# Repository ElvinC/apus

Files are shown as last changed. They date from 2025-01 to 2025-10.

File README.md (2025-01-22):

# The Apus Flight Computer (Work in progress and untested!)

Just a smol board for rockets.

Basically the [rocketbeacon](https://github.com/ElvinC/rocketbeacon) with added deployment channels and sensors.

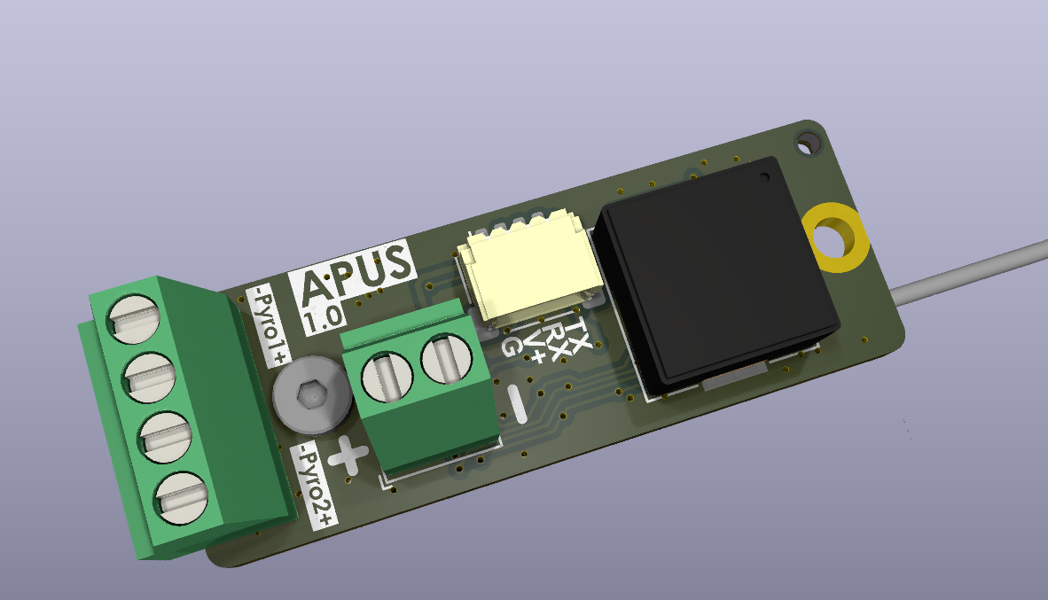
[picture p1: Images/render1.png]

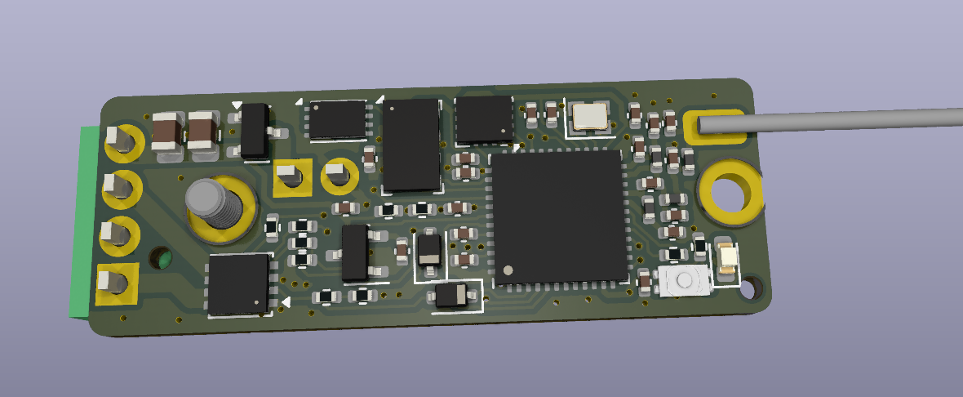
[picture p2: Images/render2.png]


Rev. 1.0 has the following hardware:

* STM32WLE5 MCU Built-in sub-GHz transceiver (for telemetry or RDF) tuned for the 440MHz band
* 2x pyro deployment channels with continuity detection
* 16Mbit flash (W25Q16JVUXIQ)
* BMI270 IMU
* MS5607 Barometer
* Reverse voltage protection
* 13x36mm board size with 2x M2 mounting holes

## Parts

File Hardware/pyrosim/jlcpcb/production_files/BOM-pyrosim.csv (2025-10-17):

Comment | Designator | Footprint | LCSC | Quantity
470R | R4 | R_0603_1608Metric |  | 1
Conn_01x04_Pin | J1 | PinHeader_1x04_P2.54mm_Horizontal |  | 1
470R | R3 | R_0603_1608Metric |  | 1
LED | D1 | LED_0603_1608Metric |  | 1
470R | R2 | R_0603_1608Metric |  | 1
470R | R1 | R_0603_1608Metric |  | 1
LED | D2 | LED_0603_1608Metric |  | 1

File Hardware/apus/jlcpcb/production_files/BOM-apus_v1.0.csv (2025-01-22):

Comment | Designator | Footprint | LCSC | Quantity
STM32WLE5CBUx | U1 | QFN-48-1EP_7x7mm_P0.5mm_EP5.6x5.6mm | C1121847 | 1
1k | R10,R9 | R_0402_1005Metric | C11702 | 2
68p | C4 | C_0402_1005Metric | C14441 | 1
100u | C17,C19 | C_0805_2012Metric | C15008 | 2
AO3401A | Q1 | SOT-23 | C15127 | 1
15p | C7 | C_0402_1005Metric | C1548 | 1
10u | C1,C10,C11,C12,C13,C14,C15,C2,C3 | C_0402_1005Metric | C15525 | 9
2.7p | C6 | C_0402_1005Metric | C1561 | 1
6.8p | C8 | C_0402_1005Metric | C1576 | 1
3.6p | C20 | C_0402_1005Metric | C161321 | 1
1N5819WS | D2,D3 | D_SOD-323 | C191023 | 2
RED | D1 | LED_0603_1608Metric | C2286 | 1
10k | R1,R2,R5,R6,R7,R8 | R_0402_1005Metric | C25744 | 6
33k | R4 | R_0402_1005Metric | C25779 | 1
4k7 | R3 | R_0402_1005Metric | C25900 | 1
10n | L2 | L_0402_1005Metric | C27147 | 1
47n | C5 | C_0402_1005Metric | C272875 | 1
BMI270 | U6 | Bosch_LGA-14_3x2.5mm_P0.5mm | C2836813 | 1
W25Q16JVUXIQ | U4 | Winbond_USON-8-1EP_3x2mm_P0.5mm_EP0.2x1.6mm | C2843335 | 1
32MHz | Y1 | Crystal_SMD_2016-4Pin_2.0x1.6mm | C383840 | 1
470n | C9 | C_0402_1005Metric | C47339 | 1
1u | C16,C18 | C_0402_1005Metric | C52923 | 2
4p | C21 | C_0402_1005Metric | C541337 | 1
XC6206P332MR | U2 | SOT-23 | C5446 | 1
18n | L3 | L_0402_1005Metric | C86060 | 1
BOOT | SW1 | SW_1TS026A | C913778 | 1
Pyros | J3 | TerminalBlock_Phoenix_MPT-0,5-4-2.54_1x04_P2.54mm_Horizontal | C918122 | 1
YJQ3622A | Q2 | Vishay_PowerPAK_1212-8_Dual | C919566 | 1
68n | L1 | L_0402_1005Metric | C98000 | 1
MS5607-02BA | U3 | LGA-8_3x5mm_P1.25mm | C9900023641 | 1
Conn_01x04_Socket | J1 | JST_SH_SM04B-SRSS-TB_1x04-1MP_P1.00mm_Horizontal |  | 1
lipo | BT1 | TerminalBlock_TE_282834-2_1x02_P2.54mm_Horizontal |  | 1
30n | L4 | L_0402_1005Metric |  | 1
Buzzer | BZ1 | Buzzer_Murata_PKMCS0909E |  | 1

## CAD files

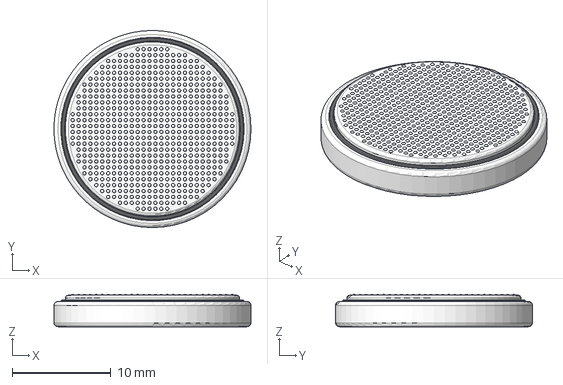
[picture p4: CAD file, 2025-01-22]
Hardware/apus/3dmodels/cr2032_cell.step
20.0 x 20.0 x 3.30 mm

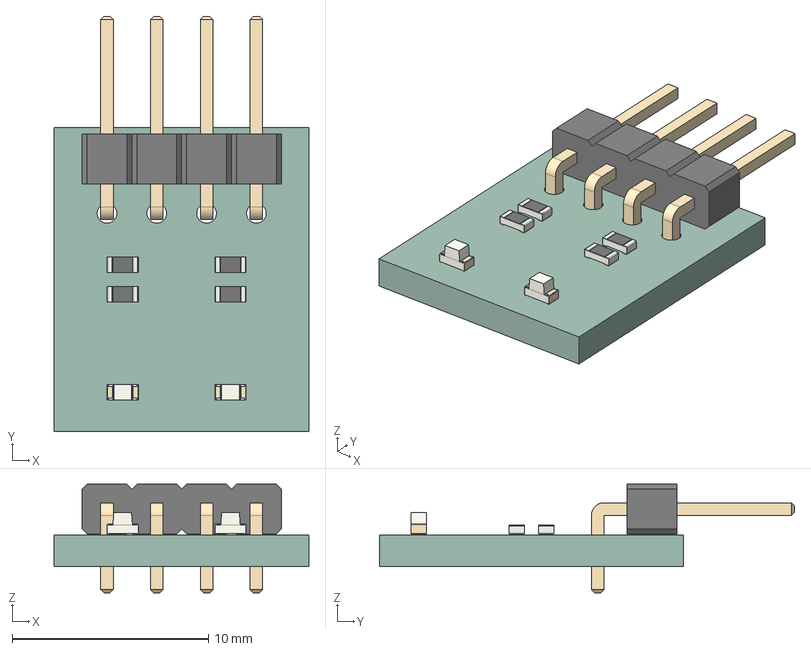
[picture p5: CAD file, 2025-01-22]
Hardware/pyrosim/pyrosim.step
13.0 x 21.2 x 5.54 mm
R_0603_1608Metric x 4
PinHeader_1x04_P254mm_Horizontal
LED_0603_1608Metric x 2
pyrosim_PCB

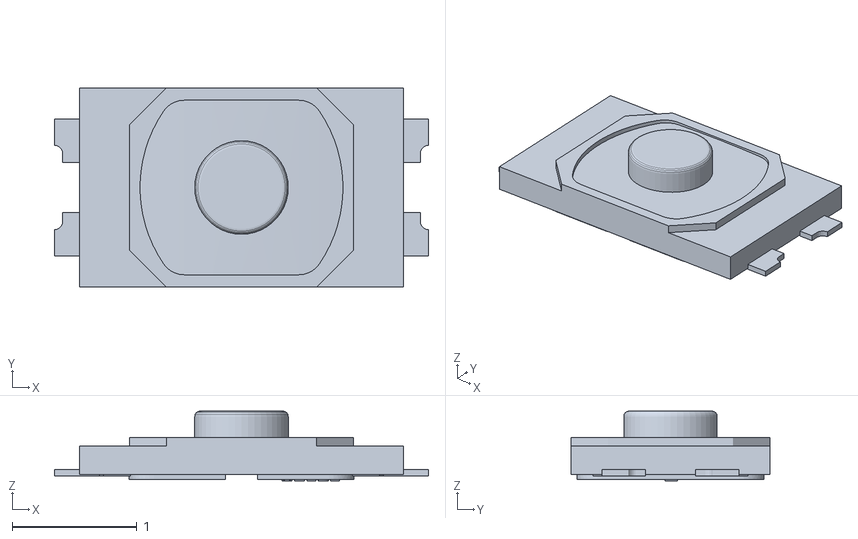
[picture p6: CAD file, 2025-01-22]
Hardware/apus/3dmodels/1TS026A-1000-0550-CT.obj
3.00 x 1.60 x 0.56

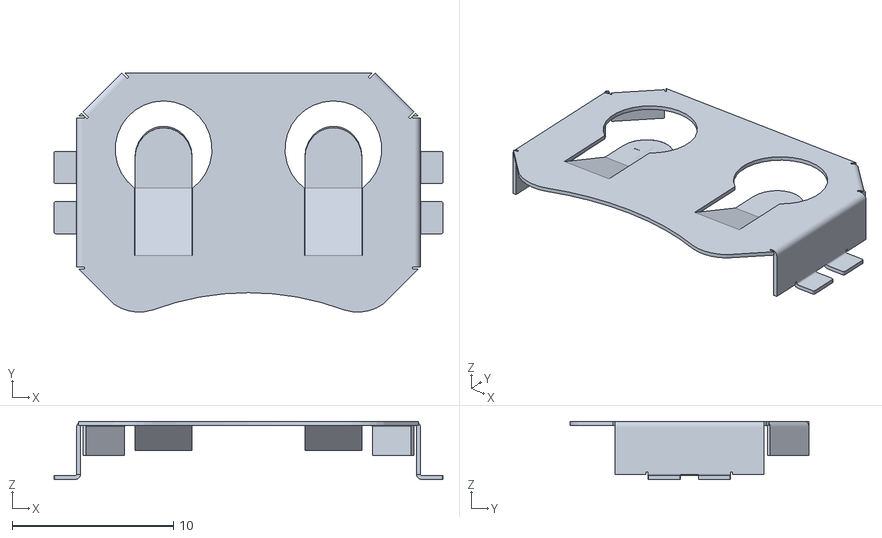
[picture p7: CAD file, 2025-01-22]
Hardware/apus/3dmodels/cr2032.obj
24.1 x 14.8 x 3.60

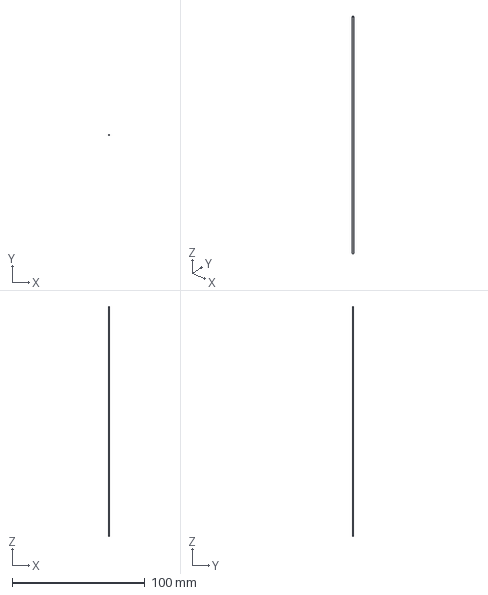
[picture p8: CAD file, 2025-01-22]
Hardware/apus/3dmodels/whipantenna.step
0.999 x 1 x 173.0 mm

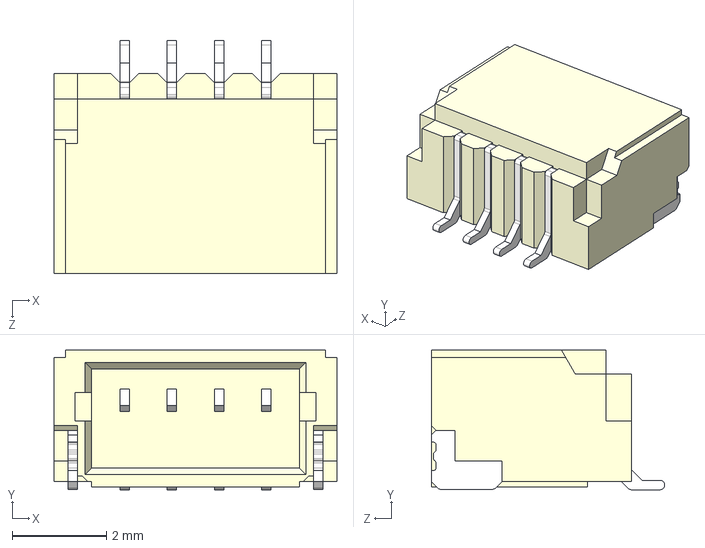
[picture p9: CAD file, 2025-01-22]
Hardware/apus/3dmodels/SM04B-SRSS-TB (LF)(SN)--3DModel-STEP-269445.STEP
6.00 x 2.96 x 4.95 mm

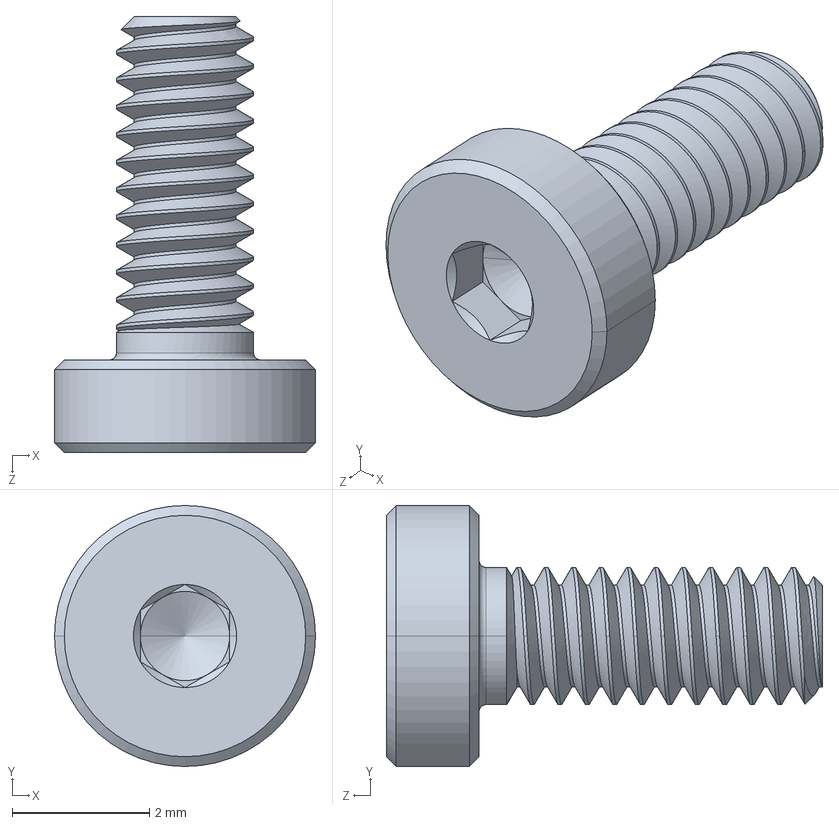
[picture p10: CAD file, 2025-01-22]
Hardware/apus/3dmodels/92855A837_18-8 Stainless Steel Low-Profile Socket Head Screws.STEP
3.80 x 3.80 x 6.35 mm

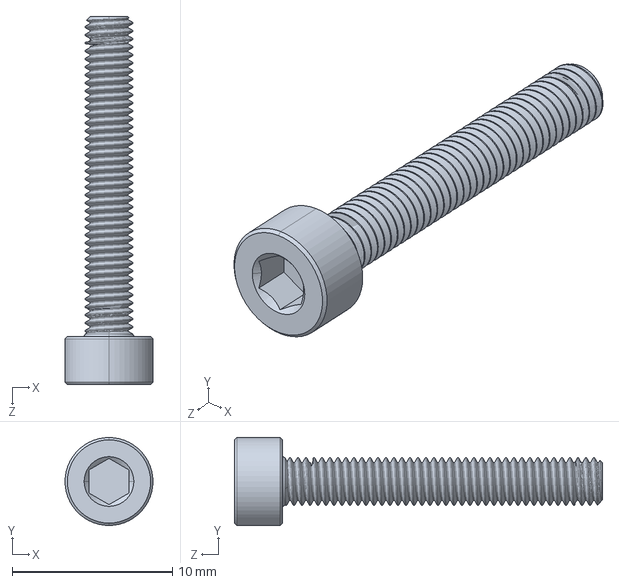
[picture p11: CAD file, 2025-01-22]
Hardware/apus/3dmodels/M3 Steel Socket Head Screw.STEP
5.50 x 5.50 x 23.0 mm

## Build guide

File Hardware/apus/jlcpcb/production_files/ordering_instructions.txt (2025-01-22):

JLCPCB Ordering options. If not specified, use defaults.

Layers=2
Thickness=1.6
Vias=Tented
Remove order number=Specify a location
PCBA type=Economic
Assembly side=Top side
Tooling holes = Added by Customer

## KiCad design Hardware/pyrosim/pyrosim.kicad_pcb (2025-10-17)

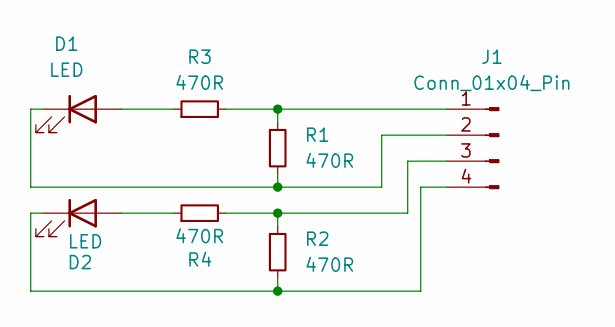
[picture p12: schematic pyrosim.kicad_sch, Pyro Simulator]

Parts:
D1, D2: LED; LED_0603_1608Metric
J1: Conn_01x04_Pin; PinHeader_1x04_P2.54mm_Horizontal
R1, R2, R3, R4: 470R; R_0603_1608Metric

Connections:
unnamed: D1.2 (A), R3.1
unnamed: D1.1 (K), J1.2, R1.2
unnamed: D2.2 (A), R4.1
unnamed: D2.1 (K), J1.4, R2.2
unnamed: J1.1, R1.1, R3.2
unnamed: J1.3, R2.1, R4.2

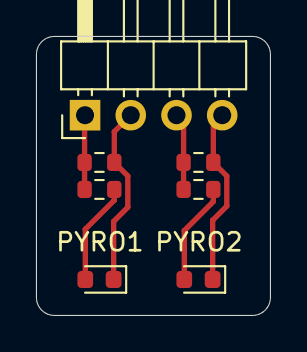
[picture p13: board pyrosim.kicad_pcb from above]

Board: 2 copper layers, 13.0 x 15.5 mm, 7 parts (0 on the bottom side), 6 nets.

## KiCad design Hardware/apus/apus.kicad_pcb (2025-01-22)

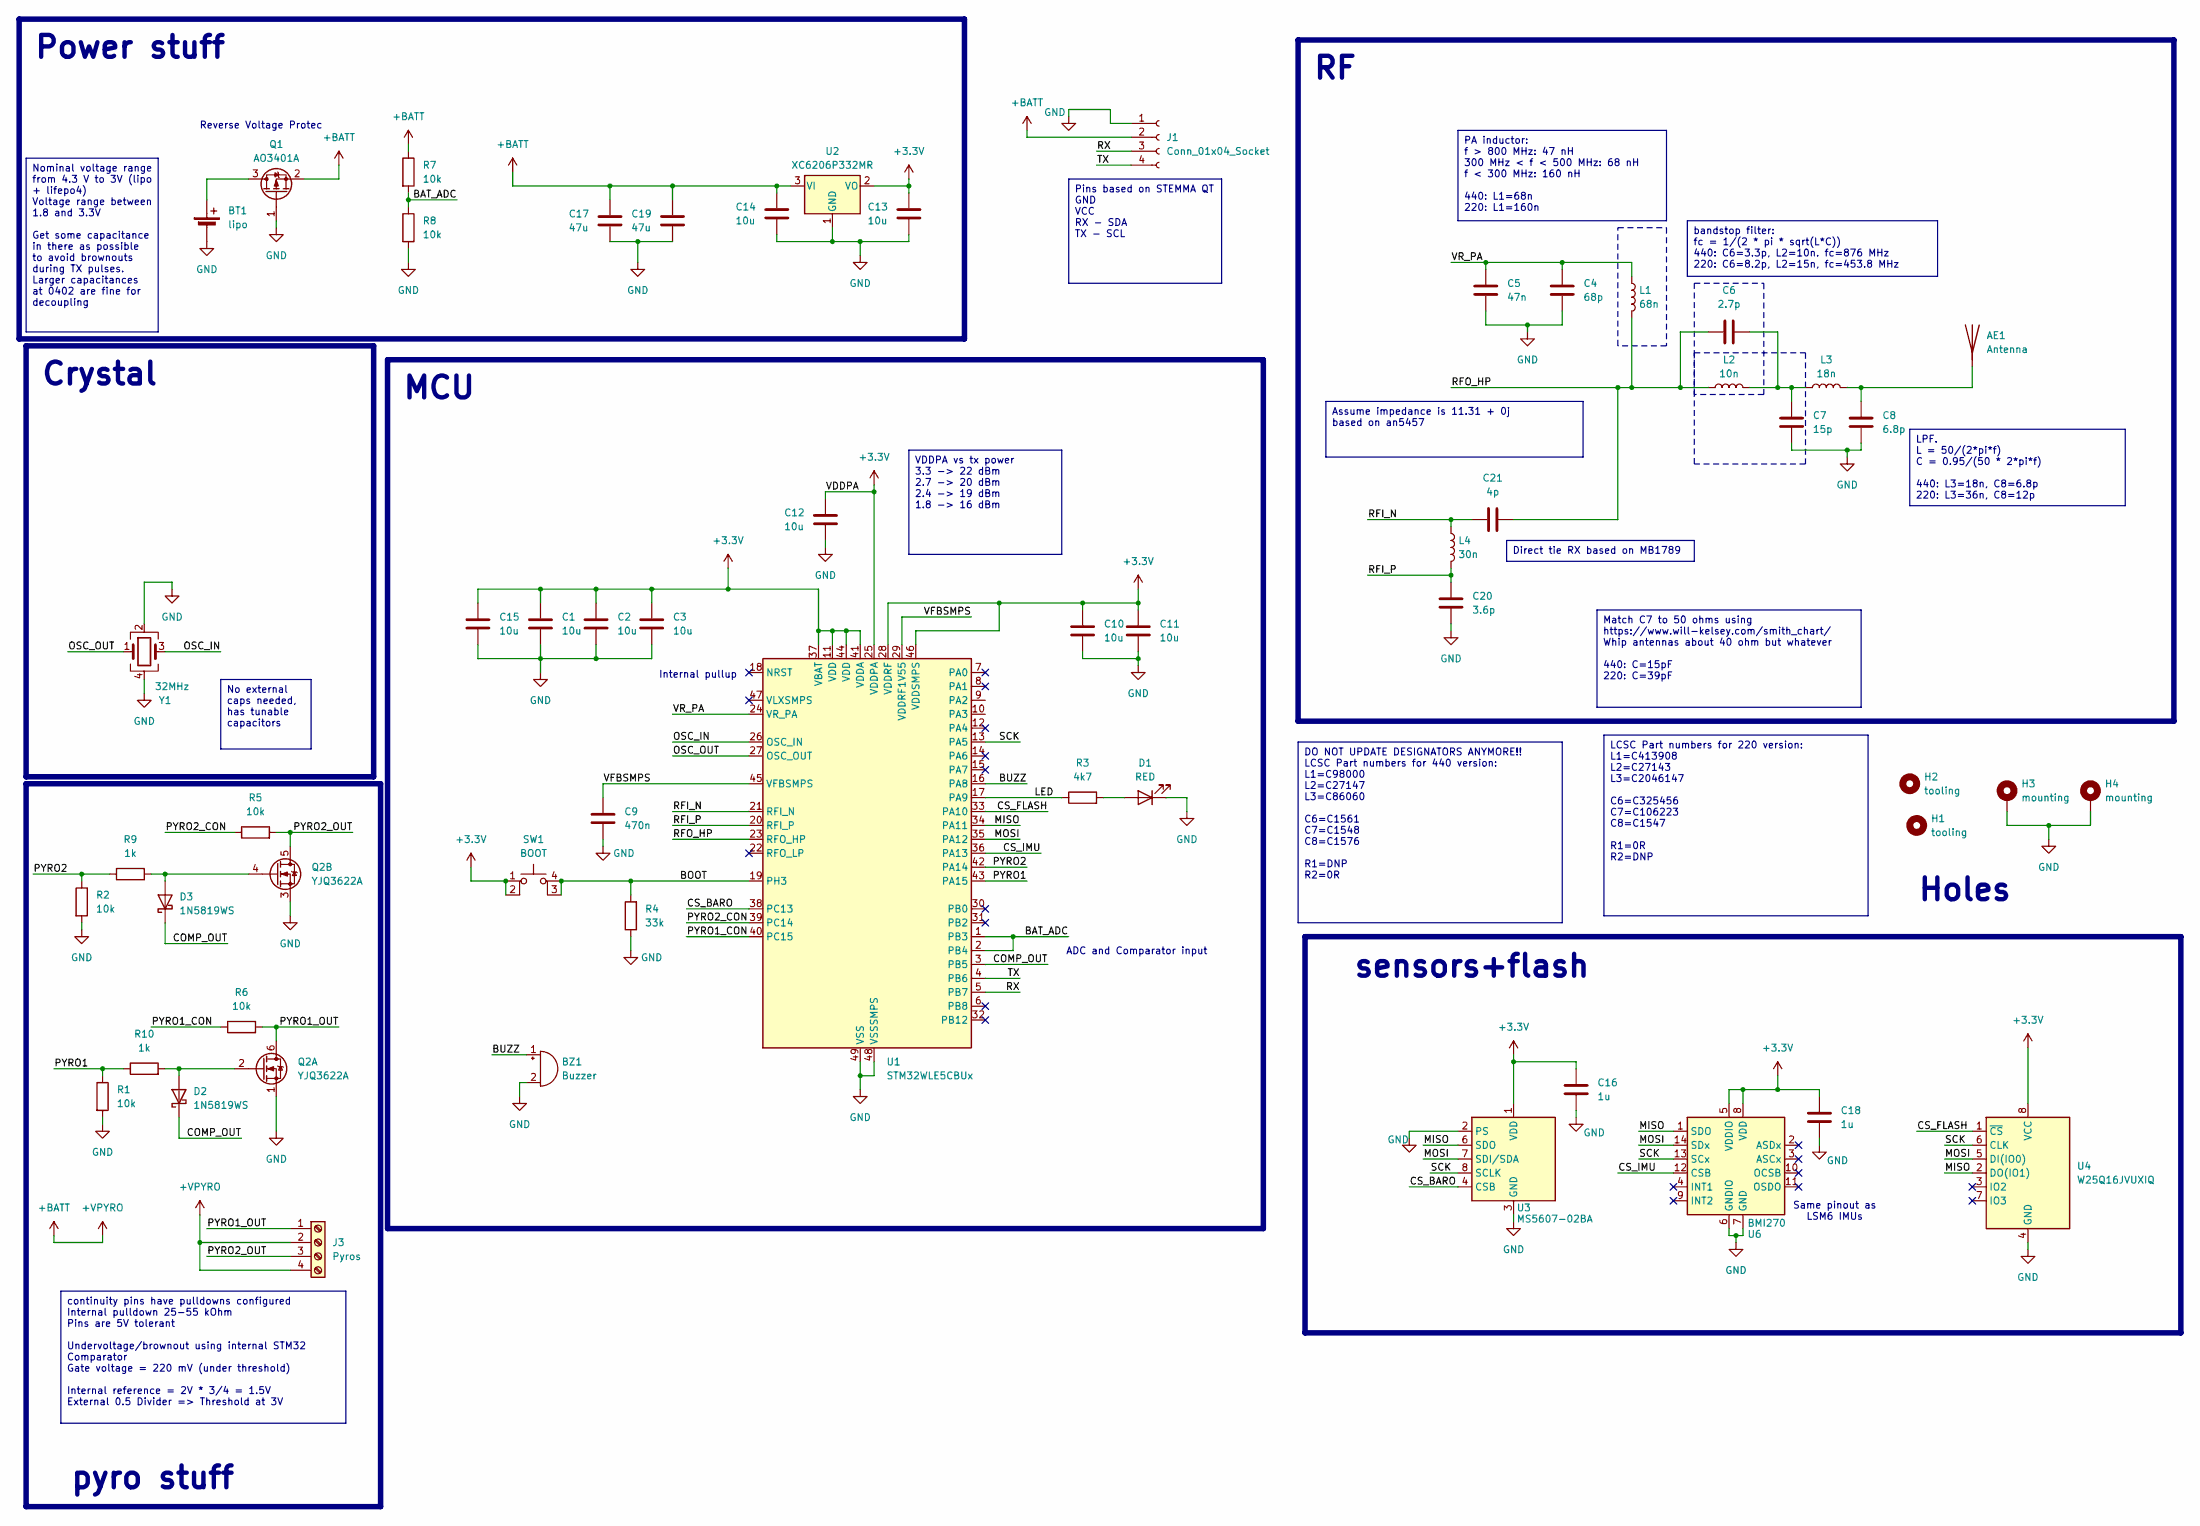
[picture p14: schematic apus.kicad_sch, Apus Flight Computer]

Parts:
AE1: Antenna; whip_antenna
BT1: lipo; TerminalBlock_TE_282834-2_1x02_P2.54mm_Horizontal
BZ1: Buzzer; Buzzer_Murata_PKMCS0909E; LCSC C96127
C1, C2, C3, C10, C11, C12, C13, C14, C15: 10u; C_0402_1005Metric
C4: 68p; C_0402_1005Metric
C5: 47n; C_0402_1005Metric
C6: 2.7p; C_0402_1005Metric
C7: 15p; C_0402_1005Metric
C8: 6.8p; C_0402_1005Metric
C9: 470n; C_0402_1005Metric
C16, C18: 1u; C_0402_1005Metric
C17, C19: 47u; C_0805_2012Metric; LCSC C16780
C20: 3.6p; C_0402_1005Metric
C21: 4p; C_0402_1005Metric
D1: RED; LED_0603_1608Metric
D2, D3: 1N5819WS; D_SOD-323
H1, H2: tooling; toolinghole
H3, H4: mounting; MountingHole_2.2mm_M2_DIN965_Pad
J1: Conn_01x04_Socket; JST_SH_SM04B-SRSS-TB_1x04-1MP_P1.00mm_Horizontal; LCSC C160404
J3: Pyros; TerminalBlock_Phoenix_MPT-0,5-4-2.54_1x04_P2.54mm_Horizontal; LCSC C918122
L1: 68n; L_0402_1005Metric
L2: 10n; L_0402_1005Metric
L3: 18n; L_0402_1005Metric
L4: 30n; L_0402_1005Metric
Q1: AO3401A; SOT-23
Q2: YJQ3622A; Vishay_PowerPAK_1212-8_Dual
R1, R2, R5, R6, R7, R8: 10k; R_0402_1005Metric
R3: 4k7; R_0402_1005Metric
R4: 33k; R_0402_1005Metric
R9, R10: 1k; R_0402_1005Metric
SW1: BOOT; SW_1TS026A
U1: STM32WLE5CBUx; QFN-48-1EP_7x7mm_P0.5mm_EP5.6x5.6mm
U2: XC6206P332MR; SOT-23
U3: MS5607-02BA; LGA-8_3x5mm_P1.25mm; LCSC C97627
U4: W25Q16JVUXIQ; Winbond_USON-8-1EP_3x2mm_P0.5mm_EP0.2x1.6mm
U6: BMI270; Bosch_LGA-14_3x2.5mm_P0.5mm
Y1: 32MHz; Crystal_SMD_2016-4Pin_2.0x1.6mm; LCSC C383840

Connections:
+3.3V: C1.1, C2.1, C3.1, C10.1, C11.1, C12.1, C13.1, C15.1, C16.1, C18.1, SW1.1, SW1.2, U1.11 (VDD), U1.25 (VDDPA), U1.28 (VDDRF), U1.37 (VBAT), U1.41 (VDDA), U1.44 (VDD), U1.46 (VDDSMPS), U2.2 (VO), U3.1 (VDD), U4.8 (VCC), U6.5 (VDDIO), U6.8 (VDD)
+BATT: C14.1, C17.1, C19.1, J1.2, J3.2, J3.4, Q1.2 (S), R7.1, U2.3 (VI)
/BAT_ADC: R7.2, R8.1, U1.1 (PB3), U1.2 (PB4)
/BOOT: R4.2, SW1.3 (K), SW1.4 (A), U1.19 (PH3)
/BUZZ: BZ1.1 (+), U1.16 (PA8)
/COMP_OUT: D2.1 (K), D3.1 (K), U1.3 (PB5)
/CS_BARO: U1.38 (PC13), U3.4 (CSB), U3.5 (CSB)
/CS_FLASH: U1.33 (PA10), U4.1 (~CS)
/CS_IMU: U1.36 (PA13), U6.12 (CSB)
/LED: R3.1, U1.17 (PA9)
/MISO: U1.34 (PA11), U3.6 (SDO), U4.2 (DO(IO1)), U6.1 (SDO)
/MOSI: U1.35 (PA12), U3.7 (SDI/SDA), U4.5 (DI(IO0)), U6.14 (SDx)
/OSC_IN: U1.26 (OSC_IN), Y1.3
/OSC_OUT: U1.27 (OSC_OUT), Y1.1
/PYRO1: R1.1, R10.1, U1.43 (PA15)
/PYRO1_CON: R6.1, U1.40 (PC15)
/PYRO1_OUT: J3.1, Q2.6 (D), R6.2
/PYRO2: R2.1, R9.1, U1.42 (PA14)
/PYRO2_CON: R5.1, U1.39 (PC14)
/PYRO2_OUT: J3.3, Q2.5 (D), R5.2
/RFI_N: C21.1, L4.1, U1.21 (RFI_N)
/RFI_P: C20.1, L4.2, U1.20 (RFI_P)
/RFO_HP: C6.1, C21.2, L1.2, L2.1, U1.23 (RFO_HP)
/RX: J1.3, U1.5 (PB7)
/SCK: U1.13 (PA5), U3.8 (SCLK), U4.6 (CLK), U6.13 (SCx)
/TX: J1.4, U1.4 (PB6)
/VFBSMPS: C9.1, U1.29 (VDDRF1V55), U1.45 (VFBSMPS)
/VR_PA: C4.1, C5.1, L1.1, U1.24 (VR_PA)
GND: BT1.2 (-), BZ1.2 (-), C1.2, C2.2, C3.2, C4.2, C5.2, C7.2, C8.2, C9.2, C10.2, C11.2, C12.2, C13.2, C14.2, C15.2, C16.2, C17.2, C18.2, C19.2, C20.2, D1.1 (K), H3.1, H4.1, J1.1, Q1.1 (G), Q2.1 (S), Q2.3 (S), R1.2, R2.2, R4.1, R8.2, U1.48 (VSSSMPS), U1.49 (VSS), U2.1 (GND), U3.2 (PS), U3.3 (GND), U4.4 (GND), U6.6 (GNDIO), U6.7 (GND), Y1.2, Y1.4
unnamed: AE1.1 (A), C8.1, L3.2
unnamed: BT1.1 (+), Q1.3 (D)
unnamed: C6.2, C7.1, L2.2, L3.1
unnamed: D1.2 (A), R3.2
unnamed: D2.2 (A), Q2.2 (G), R10.2
unnamed: D3.2 (A), Q2.4 (G), R9.2

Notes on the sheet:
No external caps needed, has tunable capacitors
Match C7 to 50 ohms using https://www.will-kelsey.com/smith_chart/ Whip antennas about 40 ohm but whatever 440: C=15pF 220: C=39pF
continuity pins have pulldowns configured Internal pulldown 25-55 kOhm Pins are 5V tolerant Undervoltage/brownout using internal STM32 Comparator Gate voltage = 220 mV (under threshold) Internal reference = 2V * 3/4 = 1.5V External 0.5 Divider => Threshold at 3V
PA inductor: f > 800 MHz: 47 nH 300 MHz < f < 500 MHz: 68 nH f < 300 MHz: 160 nH 440: L1=68n 220: L1=160n
bandstop filter: fc = 1/(2 * pi * sqrt(L*C)) 440: C6=3.3p, L2=10n. fc=876 MHz 220: C6=8.2p, L2=15n, fc=453.8 MHz
VDDPA vs tx power 3.3 -> 22 dBm 2.7 -> 20 dBm 2.4 -> 19 dBm 1.8 -> 16 dBm
LCSC Part numbers for 220 version: L1=C413908 L2=C27143 L3=C2046147 C6=C325456 C7=C106223 C8=C1547 R1=0R R2=DNP
Nominal voltage range from 4.3 V to 3V (lipo + lifepo4) Voltage range between 1.8 and 3.3V Get some capacitance in there as possible to avoid brownouts during TX pulses. Larger capacitances at 0402 are fine for decoupling
Direct tie RX based on MB1789
Assume impedance is 11.31 + 0j based on an5457
LPF. L = 50/(2*pi*f) C = 0.95/(50 * 2*pi*f) 440: L3=18n, C8=6.8p 220: L3=36n, C8=12p
Pins based on STEMMA QT GND VCC RX - SDA TX - SCL
DO NOT UPDATE DESIGNATORS ANYMORE!! LCSC Part numbers for 440 version: L1=C98000 L2=C27147 L3=C86060 C6=C1561 C7=C1548 C8=C1576 R1=DNP R2=0R
Holes
Power stuff
MCU
Crystal
sensors+flash
Internal pullup
pyro stuff
Same pinout as LSM6 IMUs
ADC and Comparator input
Reverse Voltage Protec

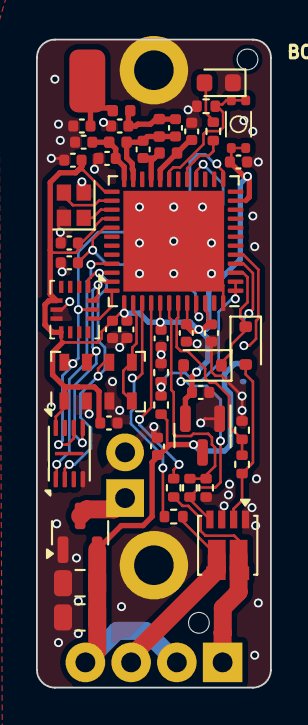
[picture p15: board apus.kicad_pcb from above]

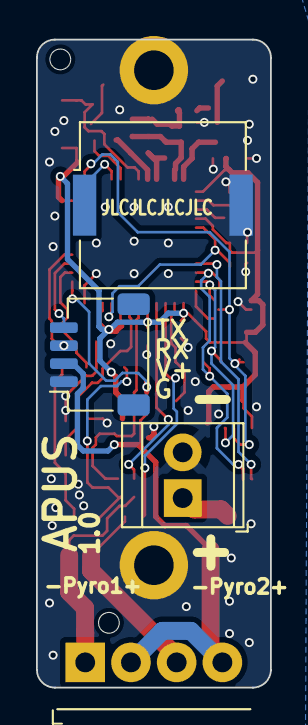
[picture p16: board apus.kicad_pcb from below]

Board: 2 copper layers, 13.0 x 36.0 mm, 56 parts (5 on the bottom side), 35 nets.

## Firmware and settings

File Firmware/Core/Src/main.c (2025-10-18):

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
/* Includes ------------------------------------------------------------------*/
#include "main.h"

/* USER CODE BEGIN Includes */
#include <stdbool.h>
#include <string.h>
#include <math.h>
#include <stdio.h>

/* USER CODE END Includes */

ADC_HandleTypeDef hadc;

COMP_HandleTypeDef hcomp2;

CRC_HandleTypeDef hcrc;

SPI_HandleTypeDef hspi1;

SUBGHZ_HandleTypeDef hsubghz;

TIM_HandleTypeDef htim2;

UART_HandleTypeDef huart2;

void SystemClock_Config(void);
static void MX_GPIO_Init(void);
static void MX_ADC_Init(void);
static void MX_CRC_Init(void);
static void MX_COMP2_Init(void);
static void MX_SPI1_Init(void);
static void MX_USART2_UART_Init(void);
static void MX_TIM2_Init(void);
/* USER CODE BEGIN PFP */

void SetStandbyXOSC();
void SetPacketTypeLora();
void SetPacketTypeFSK();
uint32_t ComputeRfFreq(double frequencyMhz);
void SetRfFreq(uint32_t rfFreq);
void SetPaLowPower();
void SetPa22dB();
void SetTxPower(int8_t powerdBm);
void SetContinuousWave();
void SetTxInfinitePreamble();
void SetTx(uint32_t timeout);
void SetRx(uint32_t timeout);
void SetModulationParamsLora(const uint8_t params[4]);
void SetModulationParamsFSK(uint32_t bitrate, uint8_t pulseshape,
		uint8_t bandwidth, uint32_t freq_dev);
void SetPacketParamsLora(uint16_t preamble_length, bool header_fixed,
		uint8_t payload_length, bool crc_enabled, bool invert_iq);
void SetPacketParamsGeneric(uint16_t preamble_length,
		uint8_t preamble_det_length, uint8_t sync_length, uint8_t addr_comp,
		uint8_t pkt_type, uint8_t payloadlength, uint8_t crc_type,
		uint8_t whitening);
void FSKBeep(int8_t powerdBm, uint32_t toneHz, uint32_t lengthMs);
void CWBeep(int8_t powerdBm, uint32_t lengthMs);

/* USER CODE END PFP */

/* USER CODE BEGIN 0 */

// standard frequencies. Note: zero indexed.
const double LPD433[69] = { 433.075, 433.100, 433.125, 433.150, 433.175,
		433.200, 433.225, 433.250, 433.275,
		433.300, // 1-10
		433.325, 433.350, 433.375, 433.400, 433.425, 433.450, 433.475, 433.500,
		433.525,
		433.550, // 11-20
		433.575, 433.600, 433.625, 433.650, 433.675, 433.700, 433.725, 433.750,
		433.775,
		433.800, // 21-30
		433.825, 433.850, 433.875, 433.900, 433.925, 433.950, 433.975, 434.000,
		434.025,
		434.050, // 31-40
		434.075, 434.100, 434.125, 434.150, 434.175, 434.200, 434.225, 434.250,
		434.275,
		434.300, // 41-50
		434.325, 434.350, 434.375, 434.400, 434.425, 434.450, 434.475, 434.500,
		434.525,
		434.550, // 51-60
		434.575, 434.600, 434.625, 434.650, 434.675, 434.700, 434.725, 434.750,
		434.775           // 61-69
		};

const double PMR446[16] = { 446.00625, 446.01875, 446.03125, 446.04375,
		446.05625, // 1-5
		446.06875, 446.08125, 446.09375, 446.10625, 446.11875, // 6-10
		446.13125, 446.14375, 446.15625, 446.16875, 446.18125, // 11-15
		446.19375 // 16
		};

const double FRS[22] = { 462.5625, 462.5875, 462.6125, 462.6375, 462.6625,
		462.6875, 462.7125, 467.5625, 467.5875,
		467.6125, // 1-10
		467.6375, 467.6625, 467.6875, 467.7125, 462.5500, 462.5750, 462.6000,
		462.6250, 462.6500, 462.6750, // 11-20
		462.7000, 462.7250 // 21-22
		};

// letter to morse based on ASCII characters.
// right-terminated by a "1". 1 is dah, 0 is dit.
const uint8_t morse_chars[] = { 0b11111111,       // Special code for SPACE
		0b10000000,       // N/A
		0b10000000,       // N/A
		0b10000000,       // N/A
		0b10000000,       // N/A
		0b10000000,       // N/A
		0b10000000,       // N/A
		0b10000000,       // N/A
		0b10000000,       // N/A
		0b10000000,       // N/A
		0b10000000,       // N/A
		0b10000000,       // N/A
		0b10000000,       // N/A
		0b10000110,       // - Hyphen sign
		0b10000000,       // N/A
		0b10010100,       // "/" Slash
		0b11111100,       // "0"
		0b01111100,       // "1"
		0b00111100,       // "2"
		0b00011100,       // "3"
		0b00001100,       // "4"
		0b00000100,       // "5"
		0b10000100,       // "6"
		0b11000100,       // "7"
		0b11100100,       // "8"
		0b11110100,       // "9"
		0b10000000,       // N/A
		0b10000000,       // N/A
		0b10000000,       // N/A
		0b10001100,       // "=" BT prosign/Equal sign
		0b10000000,       // N/A
		0b00110010,       // "?" Question mark
		0b10000000,       // N/A
		0b01100000,       // "A"
		0b10001000,       // "B"
		0b10101000,       // "C"
		0b10010000,       // "D"
		0b01000000,       // "E"
		0b00101000,       // "F"
		0b11010000,       // "G"
		0b00001000,       // "H"
		0b00100000,       // "I"
		0b01111000,       // "J"
		0b10110000,       // "K"
		0b01001000,       // "L"
		0b11100000,       // "M"
		0b10100000,       // "N"
		0b11110000,       // "O"
		0b01101000,       // "P"
		0b11011000,       // "Q"
		0b01010000,       // "R"
		0b00010000,       // "S"
		0b11000000,       // "T"
		0b00110000,       // "U"
		0b00011000,       // "V"
		0b01110000,       // "W"
		0b10011000,       // "X"
		0b10111000,       // "Y"
		0b11001000,       // "Z"
		0b10000000,       // N/A
		0b10000000,       // N/A
		0b10000000,       // N/A
		0b10000000,       // N/A
		0b10000000,       // N/A
		0b10000000,       // N/A
		0b01100000,       // "a"
		0b10001000,       // "b"
		0b10101000,       // "c"
		0b10010000,       // "d"
		0b01000000,       // "e"
		0b00101000,       // "f"
		0b11010000,       // "g"
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
		};

void LED_on() {
	HAL_GPIO_WritePin(LED_GPIO_Port, LED_Pin, GPIO_PIN_SET);
}
void LED_off() {
	HAL_GPIO_WritePin(LED_GPIO_Port, LED_Pin, GPIO_PIN_RESET);
}

void BUZZER_on() {
	HAL_GPIO_WritePin(BUZZER_GPIO_Port, BUZZER_Pin, GPIO_PIN_SET);
}
void BUZZER_off() {
	HAL_GPIO_WritePin(BUZZER_GPIO_Port, BUZZER_Pin, GPIO_PIN_RESET);
}

// https://en.wikipedia.org/wiki/Morse_code#/media/File:International_Morse_Code.svg
uint32_t morse_unit_ms = 70;
int8_t morse_power = 10;

void play_morse_char(uint8_t ascii_letter, bool use_cw) {
	uint8_t morse_code = 0b11111111;
	if (ascii_letter > 31 && ascii_letter < 123) {
		morse_code = morse_chars[ascii_letter - 32];
	}

	// space
	if (morse_code == 0b11111111) {
		if (use_cw) {
			HAL_Delay(morse_unit_ms);
		} else {
			//FSKBeep(morse_power, 750, morse_unit_ms);
			HAL_Delay(morse_unit_ms);
		}
		return;
	}
	uint8_t terminatelen = 0;
	for (uint8_t idx = 0; idx < 8; idx++) {
		if (morse_code & (1 << idx)) {
			terminatelen = idx;
			break;
		}
	}

	for (uint8_t i = 7; i > terminatelen; i--) {
		LED_on();
		if (morse_code & (1 << i)) {
			// make dat
			//printf("-");
			if (use_cw) {
				CWBeep(morse_power, morse_unit_ms * 3);
			} else {
				FSKBeep(morse_power, 400, morse_unit_ms * 3);
			}
		} else {
			// make dit
			//printf(".");
			if (use_cw) {
				CWBeep(morse_power, morse_unit_ms);
			} else {
				FSKBeep(morse_power, 400, morse_unit_ms);
			}
		}
		LED_off();

		// Make delay.
		if (use_cw) {
			HAL_Delay(morse_unit_ms);
		} else {
			HAL_Delay(morse_unit_ms);
			//CWBeep(morse_power, morse_unit_ms);
		}
	}
}

void play_morse_word(uint8_t *letters, uint8_t len, bool use_cw) {
	for (uint8_t i = 0; i < len; i++) {
		play_morse_char(letters[i], use_cw);

		// Space between letters
		if (use_cw) {
			HAL_Delay(morse_unit_ms * 3);
		} else {
			//CWBeep(morse_power, morse_unit_ms);
			HAL_Delay(morse_unit_ms * 3);
		}
	}
}

void rx_test(bool is_tx) {
	LED_on();
	HAL_Delay(100);
	LED_off();
	SetStandbyXOSC();
	HAL_Delay(1);
	SetPacketTypeLora();
	HAL_Delay(1);
	SetRfFreq(ComputeRfFreq(433.250));

	//SetPaLowPower(); // For powers up to 14 dBm
	SetPa22dB(); // Allows powers up to 22 dBm
	HAL_Delay(1);
	SetTxPower(-9);
	HAL_Delay(1);
	uint8_t LORA_SF12_BW62_CR45[4] = { 0x0C, 0x03, 0x01, 0x00 };
	SetModulationParamsLora(LORA_SF12_BW62_CR45);
	HAL_Delay(1);

	SetPacketParamsLora(4, true, 4, true, false); // Send 4 bytes
	HAL_Delay(1);
	uint8_t buffer[4] = { 0x00, 0x00, 0x00, 0x00 };
	HAL_SUBGHZ_WriteBuffer(&hsubghz, 0, buffer, 4);

	while (1) {
		if (is_tx) {
			buffer[0] = 0x04; // Led ON
			HAL_SUBGHZ_WriteBuffer(&hsubghz, 0, buffer, 4);
			HAL_Delay(1);
			SetTx(0);
			LED_on();
			HAL_Delay(1000);

		} else {
			SetRx(0);
			HAL_Delay(100);
			HAL_SUBGHZ_ReadBuffer(&hsubghz, 0, buffer, 4);
			if (buffer[0] == 0x04) {
				LED_on();

			} else {
				LED_off();
			}
		}
	}

}

/*! @name  Global array that stores the configuration file of BMI270 */
const uint8_t bmi270_maximum_fifo_config_file[] = { 0xc8, 0x2e, 0x00, 0x2e,
		0x80, 0x2e, 0x1a, 0x00, 0xc8, 0x2e, 0x00, 0x2e, 0xc8, 0x2e, 0x00, 0x2e,
		0xc8, 0x2e, 0x00, 0x2e, 0xc8, 0x2e, 0x00, 0x2e, 0xc8, 0x2e, 0x00, 0x2e,
		0xc8, 0x2e, 0x00, 0x2e, 0x90, 0x32, 0x21, 0x2e, 0x59, 0xf5, 0x10, 0x30,
		0x21, 0x2e, 0x6a, 0xf5, 0x1a, 0x24, 0x22, 0x00, 0x80, 0x2e, 0x3b, 0x00,
		0xc8, 0x2e, 0x44, 0x47, 0x22, 0x00, 0x37, 0x00, 0xa4, 0x00, 0xff, 0x0f,
		0xd1, 0x00, 0x07, 0xad, 0x80, 0x2e, 0x00, 0xc1, 0x80, 0x2e, 0x00, 0xc1,
		0x80, 0x2e, 0x00, 0xc1, 0x80, 0x2e, 0x00, 0xc1, 0x80, 0x2e, 0x00, 0xc1,
		0x80, 0x2e, 0x00, 0xc1, 0x80, 0x2e, 0x00, 0xc1, 0x80, 0x2e, 0x00, 0xc1,
		0x80, 0x2e, 0x00, 0xc1, 0x80, 0x2e, 0x00, 0xc1, 0x80, 0x2e, 0x00, 0xc1,
		0x00, 0x00, 0x00, 0x00, 0x00, 0x00, 0x11, 0x24, 0xfc, 0xf5, 0x80, 0x30,
		0x40, 0x42, 0x50, 0x50, 0x00, 0x30, 0x12, 0x24, 0xeb, 0x00, 0x03, 0x30,
		0x00, 0x2e, 0xc1, 0x86, 0x5a, 0x0e, 0xfb, 0x2f, 0x21, 0x2e, 0xfc, 0xf5,
		0x13, 0x24, 0x63, 0xf5, 0xe0, 0x3c, 0x48, 0x00, 0x22, 0x30, 0xf7, 0x80,
		0xc2, 0x42, 0xe1, 0x7f, 0x3a, 0x25, 0xfc, 0x86, 0xf0, 0x7f, 0x41, 0x33,
		0x98, 0x2e, 0xc2, 0xc4, 0xd6, 0x6f, 0xf1, 0x30, 0xf1, 0x08, 0xc4, 0x6f,
		0x11, 0x24, 0xff, 0x03, 0x12, 0x24, 0x00, 0xfc, 0x61, 0x09, 0xa2, 0x08,
		0x36, 0xbe, 0x2a, 0xb9, 0x13, 0x24, 0x38, 0x00, 0x64, 0xbb, 0xd1, 0xbe,
		0x94, 0x0a, 0x71, 0x08, 0xd5, 0x42, 0x21, 0xbd, 0x91, 0xbc, 0xd2, 0x42,
		0xc1, 0x42, 0x00, 0xb2, 0xfe, 0x82, 0x05, 0x2f, 0x50, 0x30, 0x21, 0x2e,
		0x21, 0xf2, 0x00, 0x2e, 0x00, 0x2e, 0xd0, 0x2e, 0xf0, 0x6f, 0x02, 0x30,
		0x02, 0x42, 0x20, 0x26, 0xe0, 0x6f, 0x02, 0x31, 0x03, 0x40, 0x9a, 0x0a,
		0x02, 0x42, 0xf0, 0x37, 0x05, 0x2e, 0x5e, 0xf7, 0x10, 0x08, 0x12, 0x24,
		0x1e, 0xf2, 0x80, 0x42, 0x83, 0x84, 0xf1, 0x7f, 0x0a, 0x25, 0x13, 0x30,
		0x83, 0x42, 0x3b, 0x82, 0xf0, 0x6f, 0x00, 0x2e, 0x00, 0x2e, 0xd0, 0x2e,
		0x12, 0x40, 0x52, 0x42, 0x00, 0x2e, 0x12, 0x40, 0x52, 0x42, 0x3e, 0x84,
		0x00, 0x40, 0x40, 0x42, 0x7e, 0x82, 0xe1, 0x7f, 0xf2, 0x7f, 0x98, 0x2e,
		0x6a, 0xd6, 0x21, 0x30, 0x23, 0x2e, 0x61, 0xf5, 0xeb, 0x2c, 0xe1, 0x6f };
#define IMU_READ_FLAG 0x80

typedef struct {
	SPI_HandleTypeDef *hspi;
	GPIO_TypeDef *cs_gpio_port;
	uint16_t cs_pin;

	uint8_t txbuf[14];
	uint8_t rxbuf[14];

	int16_t gyro_raw[3];
	int16_t acc_raw[3];

	float gyroRPS[3];
	float accMPS[3];
} BMI270;

static inline void BMI270_Wait(void) {
	__NOP();
	__NOP();
	__NOP();
	__NOP();
	__NOP();__NOP(); // At least 40 ns
}

uint8_t BMI270_ReadRegister(BMI270 *imu, uint8_t reg) {
	uint8_t txbuf[3] = { IMU_READ_FLAG | reg, 0x00, 0x00 };
	uint8_t rxbuf[3] = { 0 };

	HAL_GPIO_WritePin(imu->cs_gpio_port, imu->cs_pin, GPIO_PIN_RESET);
	BMI270_Wait();
	HAL_SPI_TransmitReceive(imu->hspi, txbuf, rxbuf, 3, HAL_MAX_DELAY);
	BMI270_Wait();
	HAL_GPIO_WritePin(imu->cs_gpio_port, imu->cs_pin, GPIO_PIN_SET);

	return rxbuf[2];
}

void BMI270_WriteRegister(BMI270 *imu, uint8_t reg, uint8_t data) {
	uint8_t txbuf[2] = { reg, data };
	uint8_t rxbuf[2] = { 0 };

	HAL_GPIO_WritePin(imu->cs_gpio_port, imu->cs_pin, GPIO_PIN_RESET);
	BMI270_Wait();
	HAL_SPI_TransmitReceive(imu->hspi, txbuf, rxbuf, 2, HAL_MAX_DELAY);
	BMI270_Wait();
	HAL_GPIO_WritePin(imu->cs_gpio_port, imu->cs_pin, GPIO_PIN_SET);
}

void BMI270_WriteConfig(BMI270 *imu) {
	uint8_t txbuf[1] = { 0x5E };
	uint8_t rxbuf[1] = { 0 };

	HAL_GPIO_WritePin(imu->cs_gpio_port, imu->cs_pin, GPIO_PIN_RESET);
	BMI270_Wait();
	HAL_SPI_TransmitReceive(imu->hspi, txbuf, rxbuf, 1, HAL_MAX_DELAY);
	HAL_SPI_Transmit(imu->hspi, bmi270_maximum_fifo_config_file,
			sizeof(bmi270_maximum_fifo_config_file), HAL_MAX_DELAY);
	BMI270_Wait();
	HAL_GPIO_WritePin(imu->cs_gpio_port, imu->cs_pin, GPIO_PIN_SET);
	BMI270_Wait();
}

void BMI270_Init(BMI270 *imu, SPI_HandleTypeDef *hspi, GPIO_TypeDef *cs_gpio,
		uint16_t cs_pin) {
	imu->hspi = hspi;
	imu->cs_gpio_port = cs_gpio;
	imu->cs_pin = cs_pin;

	HAL_Delay(20);
	BMI270_ReadRegister(imu, 0x00); // SPI dummy read
	HAL_Delay(10);

	BMI270_WriteRegister(imu, 0x7C, 0x00); // Disable power config
	HAL_Delay(1);
	BMI270_WriteRegister(imu, 0x59, 0x00); // Prepare config load
	HAL_Delay(1);
	BMI270_WriteConfig(imu);
	HAL_Delay(1);
	BMI270_WriteRegister(imu, 0x59, 0x01); // Complete config
	HAL_Delay(50);

	BMI270_WriteRegister(imu, 0x7D, 0x0E); // Enable accel, gyro, temp
	HAL_Delay(1);
	BMI270_WriteRegister(imu, 0x40, 0b10101100);
	HAL_Delay(1);
	BMI270_WriteRegister(imu, 0x42, 0b11101101);
	HAL_Delay(1);
	BMI270_WriteRegister(imu, 0x7C, 0x02); // Disable power saving
	HAL_Delay(1);
	BMI270_WriteRegister(imu, 0x43, 0x00); // Set gyro range to +/-2000dps
	HAL_Delay(1);
	BMI270_WriteRegister(imu, 0x41, 0x03); // Set acc range to +/- 16g

	imu->txbuf[0] = IMU_READ_FLAG | 0x0C;
}
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
int main(void) {
	/* MCU Configuration--------------------------------------------------------*/

	/* Reset of all peripherals, Initializes the Flash interface and the Systick. */
	HAL_Init();

	/* Configure the system clock */
	SystemClock_Config();

	/* Initialize all configured peripherals */
	MX_GPIO_Init();
	MX_ADC_Init();
	MX_CRC_Init();
	MX_COMP2_Init();
	MX_SPI1_Init();
	MX_USART2_UART_Init();
	MX_TIM2_Init();
	/* USER CODE BEGIN 2 */
	MX_SUBGHZ_Init();

	// Enable timer 2
	HAL_TIM_Base_Start(&htim2);

	// ==========================================
	//      START CHANGING SETTINGS HERE
	// ==========================================
	// Frequency setting in MHz
	// Can be a "standard" frequency, e.g. center_freq = LPD433[20-1]; sets it to LPD433 channel 20 (zero indexed) = 433.550 MHz
	double center_freq = 433.200;

	// max power in dBm, valid values between -9 and 22;
	// If using coin cell batteries, values above 16 dBm are not recommended without testing due to current limitations.
	// Alternatively use external LiPo power
	int maxPower = 0;

	double freq_correction = 0.99999539941; // For tuning frequency

	bool CallsignTF = false;
	uint8_t callsign[] = "nocall";

	int CallsignPeriod = 300; // seconds

	// Continuous Wave (CW) settings
	bool CWbeep = false;
	int CWbeepcount = 4;
	bool CWHigh2Low = true; //if true, start with highest power beep, decrease from there
	int CWbeepOffset = 150; //Hertz
	int CWbeepIndLength = 20; //milliseconds
	int CWbeepGapLength = 20; //milliseconds

	// Frequency-shift keying (FSK) settings. Can be heard with FM receivers
	bool FSKbeep = true;
	int FSKbeepcount = 3;
	bool FSKHigh2Low = false; //if true, start with highest power beep, decrease from there. When true, it maximizes the power of the highest power beep, but makes it harder to read a visible signal indicator on later beeps.
	int FSKbeepIndLength = 250; //milliseconds
	int FSKbeepGapLength = 50; //milliseconds
	bool CustomFSKtones = false;
	int CustomFSKfrequencies[] = { 320, 400, 480, 640 }; // Must match the length exactly!

	int Period = 2000; //milliseconds
	int StartupWait = 5000; // initial start. A few seconds to allow coin cell batteries to recover in case of brownout resets.

	// Set up pins
	HAL_GPIO_WritePin(CS_BARO_GPIO_Port, CS_BARO_Pin, GPIO_PIN_SET);
	HAL_GPIO_WritePin(CS_FLASH_GPIO_Port, CS_FLASH_Pin, GPIO_PIN_SET);
	HAL_GPIO_WritePin(CS_IMU_GPIO_Port, CS_IMU_Pin, GPIO_PIN_SET);

	// BMI270 instance
	BMI270 imu;
	BMI270_Init(&imu, &hspi1, CS_IMU_GPIO_Port, CS_IMU_Pin);

	// Barometer
	MS5607 baro;
	MS5607_Init(&baro, &hspi1, CS_BARO_GPIO_Port, CS_BARO_Pin);

	char printbuffer[128];

	// ==========================================
	//      STOP CHANGING SETTINGS HERE
	// ==========================================

	//EE_Status ee_status = EE_OK;
	LED_on();
	HAL_Delay(StartupWait);
	LED_off();
	SetStandbyXOSC();
	HAL_Delay(1);
	SetPacketTypeLora();
	HAL_Delay(1);

	//SetPaLowPower(); // For powers up to 14 dBm
	SetPa22dB(); // Allows powers up to 22 dBm
	HAL_Delay(1);
	SetTxPower(-9);
	HAL_Delay(1);

	SetPacketTypeFSK();

	SetModulationParamsFSK(2000, 0x09, 0x1E, 2500);

	//  int FSKtones[12] = {400, 350, 300, 250, 200, 150, 1600, 2000, 2400, 3200, 4000, 4800};
	int FSKtones[FSKbeepcount];
	SetRfFreq(ComputeRfFreq(center_freq * freq_correction));

	memset(FSKtones, 0, sizeof(FSKtones));
	for (int i = 0; i < FSKbeepcount; i++) {
		int base = floor(i / 3);
		int mplr = 1 << base;
		FSKtones[i] = 320 * (1 + 0.25 * (i - 3 * floor(i / 3))) * mplr;
	}
	if (CustomFSKtones) {
		memcpy(FSKtones, CustomFSKfrequencies, sizeof(FSKtones));
	}

	/* USER CODE END 2 */

	/* Infinite loop */
	/* USER CODE BEGIN WHILE */

	while (1) {
		long_packet_test(433.200);
		HAL_Delay(3000);
	}


	/*
	 while (1) {
	 // Emulate comspec beacon at 40 mW
	 LED_on();
	 CWBeep(16, 50);
	 LED_off();
	 HAL_Delay(1000);
	 }*/

	int loopCounter = floor(CallsignPeriod * 1000 / Period);

	int gap = Period;
	if (FSKbeep) {
		gap = gap - (FSKbeepIndLength * FSKbeepcount);
		gap = gap - (FSKbeepGapLength * (FSKbeepcount - 1));
	}
	if (CWbeep) {
		gap = gap - (CWbeepIndLength * CWbeepcount);
		gap = gap - (CWbeepGapLength * (CWbeepcount - 1));
	}
	if (CWbeep && FSKbeep) {
		gap = gap / 2;
	}

	int FSKTXpwrs[FSKbeepcount];
	memset(FSKTXpwrs, 0, sizeof(FSKTXpwrs));
	if (FSKbeep) {
		int stepsize = 0;
		if (FSKbeepcount > 1) {
			stepsize = (31 - 22 + maxPower) / (FSKbeepcount - 1);
		}
		for (int i = 0; i < FSKbeepcount; i++) {
			FSKTXpwrs[i] = maxPower - stepsize * i;
		}
	}
	int CWTXpwrs[CWbeepcount];
	memset(CWTXpwrs, 0, sizeof(CWTXpwrs));
	if (CWbeep) {
		int stepsize = 0;
		if (CWbeepcount > 1) {
			stepsize = (31 - 22 + maxPower) / (CWbeepcount - 1);
		}
		for (int i = 0; i < CWbeepcount; i++) {
			CWTXpwrs[i] = maxPower - stepsize * i;
		}
	}

	while (0) {

		LED_on();
		BUZZER_on();
		HAL_Delay(10);
		BUZZER_off();
		HAL_Delay(190);
		LED_off();
		HAL_Delay(3000);

		// Read raw gyro and accelerometer data
		BMI270_ReadGyroAccRaw(&imu);

		// Convert raw data to meaningful values
		BMI270_ConvertGyroAccToFloat(&imu);

		// Example: Print values (replace with your debug method)
		snprintf(printbuffer, 128, "Gyro (RPS): X=%f, Y=%f, Z=%f\n",
				imu.gyroRPS[0], imu.gyroRPS[1], imu.gyroRPS[2]);
		HAL_UART_Transmit(&huart2, (uint8_t*) printbuffer, strlen(printbuffer),
		HAL_MAX_DELAY);

		snprintf(printbuffer, 128, "Acc (m/s²): X=%f, Y=%f, Z=%f\n",
				imu.accMPS[0], imu.accMPS[1], imu.accMPS[2]);
		HAL_UART_Transmit(&huart2, (uint8_t*) printbuffer, strlen(printbuffer),
		HAL_MAX_DELAY);

		snprintf(printbuffer, 128, "Testregister: %d\n",
				BMI270_ReadRegister(&imu, 0x6C));
		HAL_UART_Transmit(&huart2, (uint8_t*) printbuffer, strlen(printbuffer),
		HAL_MAX_DELAY);

		MS5607_Read_Blocking(&baro);
		snprintf(printbuffer, 128, "pres raw: %ld\n", baro.pres_raw);
		HAL_UART_Transmit(&huart2, (uint8_t*) printbuffer, strlen(printbuffer),
		HAL_MAX_DELAY);

		bool APRS = true;

		HAL_Delay(100); // Delay 100ms

		// Radio stuff
		if (APRS) {

			// https://notblackmagic.com/bitsnpieces/afsk/
			// https://hugosprojects.wordpress.com/2014/03/25/implementing-aprs-message-at-the-bit-level/
			// LSB transmitted first
			uint32_t tone_one = 1200 * 2;
			uint32_t tone_zero = 2200 * 2;
			uint32_t bitrate = 1200; // Bits per second
			/*
			 uint8_t aprs_data[] = {0x00,0x00,0x00,0x00,0x00,0x00,0x00,0x00,0x00,0x00,0x00,0x00,0x00,0x00,0x00,0x00,0x00,0x00,0x00,0x00,0x00,0x00,0x00,0x00,0x00,0x00,0x00,0x00, // Buffer
			 0x7E, 'N', '0', 'C', 'A', 'L', ' ', '1',
			 'N', '0', 'C', 'A', 'L', ' ', '7',
			 0x03, 0xF0, 'H', 'E', 'L', 'L', 'O', ' ', 'W', 'O', 'R', 'L', 'D', '!',
			 0xAA, 0xAA, // Frame check bytes, not calculated
			 0x7E, 0xFF, 0xFF, 0xFF, 0xFF, 0xFF, 0xFF, 0xFF, 0xFF, 0xFF, 0xFF, 0xFF, 0xFF, 0xFF, 0xFF, 0xFF, 0xFF, 0xFF, 0xFF, 0xFF, 0xFF, 0xFF, 0xFF, 0xFF}; // End of frame
			 */
			// Must be 7 characters long, with the SSID (number) on the 7th
			char dest_address[] = "NOCALL1";
			char source_address[] = "NOCALL7";
			char addressee[] = "YOU"; // Will be padded to 9 chars
			char message[128];
			snprintf(message, 128,
					":%-9s:Hello World from Apus! This required: C>Python>C>Apus>Radio>Mic>APRS Decoder. AccX:%.2f",
					addressee, imu.accMPS[0]);
			//char message[] = "Hello world from Apus! This screenshot required: C>Python>C>Apus>Radio>Mic>APRS Decoder. AccX:";

			char content_formatted[256];
			uint16_t content_pointer = 0;

			for (int i = 0; i < strlen(dest_address); i++) {
				content_formatted[content_pointer++] = dest_address[i] << 1;
			}

			for (int i = 0; i < (strlen(source_address) - 1); i++) {
				content_formatted[content_pointer++] = source_address[i] << 1;
			}

			// Set LSB
			content_formatted[content_pointer++] = (source_address[strlen(
					source_address) - 1] << 1) | 0x01;

			//
			content_formatted[content_pointer++] = 0x03; // Control Field
			content_formatted[content_pointer++] = 0xF0; // Protocol ID

			for (int i = 0; i < strlen(message); i++) {
				content_formatted[content_pointer++] = message[i];
			}

			uint16_t crc;
			crc = sysCRC16(content_formatted, content_pointer, 0xffff);

			content_formatted[content_pointer++] = ((crc) & 0xFF);
			content_formatted[content_pointer++] = ((crc >> 8) & 0xFF);

			// 3 bit frequency lookup table for sine
			double deviation = 0.003; // deviation in megahertz
			uint32_t f_lut[8];
			for (int i = 0; i < 8; i++) {
				f_lut[i] = ComputeRfFreq(
						center_freq
								+ 0.5 * deviation
										* sin(2.0 * M_PI * (double) i / 8.0));
			}

			// Numerically controlled oscillator
			uint16_t NCO_accumulator = 0;
			uint16_t NCO_addition = 0x2000;
			uint16_t delta_1200 = 0x2000;
			uint16_t delta_2200 = 0x3aab;
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

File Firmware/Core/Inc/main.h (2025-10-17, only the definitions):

#define BUZZER_Pin GPIO_PIN_8
#define BUZZER_GPIO_Port GPIOA
#define LED_Pin GPIO_PIN_9
#define LED_GPIO_Port GPIOA
#define BOOT_Pin GPIO_PIN_3
#define BOOT_GPIO_Port GPIOH
#define CS_FLASH_Pin GPIO_PIN_10
#define CS_FLASH_GPIO_Port GPIOA
#define CS_IMU_Pin GPIO_PIN_13
#define CS_IMU_GPIO_Port GPIOA
#define CS_BARO_Pin GPIO_PIN_13
#define CS_BARO_GPIO_Port GPIOC
#define PYRO2_CON_Pin GPIO_PIN_14
#define PYRO2_CON_GPIO_Port GPIOC
#define PYRO1_CON_Pin GPIO_PIN_15
#define PYRO1_CON_GPIO_Port GPIOC
#define PYRO2_Pin GPIO_PIN_14
#define PYRO2_GPIO_Port GPIOA
#define PYRO1_Pin GPIO_PIN_15
#define PYRO1_GPIO_Port GPIOA

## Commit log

2025-01-22 Initial commit with 1.0 files
    [1TS026A-1000-0550-CT.obj, 92855A837_18-8 Stainless Steel Low-Profile Socket Head Screws.STEP, BOM-apus_v1.0.csv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]
2025-10-17 APRS emulation testing, trying to get long packets working
    [BOM-pyrosim.csv, apus.kicad_sch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]

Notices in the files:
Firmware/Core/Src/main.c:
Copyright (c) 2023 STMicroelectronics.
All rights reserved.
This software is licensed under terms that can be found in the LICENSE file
